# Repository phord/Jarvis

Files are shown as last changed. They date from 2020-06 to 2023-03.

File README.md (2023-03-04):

**Me:** Ok, Google. Stand up.<br/>
**Google Assistant:**  Ok. Raising your Jarvis desk.<br/>
**Desk:** _begins moving obediently_<br/>

# IoT Jarvis standup desk interface

**Notice:** This project probably will void your warranty.  Proceed at your own risk.

This is a project to add a computer interface to my [Jarvis stand-up desk from fully.com](https://www.fully.com/standing-desks/jarvis.html).
I reverse-engineered the interface between the desk handset and the desk controller box
to find out how they communicate. Then I wired an ESP8266 wifi module (like the [Huzzah
from Adafruit](https://www.adafruit.com/product/2471)) to a couple of RJ-45
jacks and plugged it all together.  Now I can snoop on the messages being sent between
the desk and the handset, inject my own messages to either one, and monitor the desk position
from the internet using the AdafruitIO MQTT dashboard interface.

It's pretty cool, but honestly, my motivation was to be able to lower the desk without getting
up to see the handset controller. The desk sits next to my couch at home. When I want to set
a drink on it while watching TV, it's inconvenient if I left it standing up.  "Ok, Google. Sit down"
The desk lowers, and I can put my drink down and continue watching Netflix. To be fair, I didn't need to
decode the serial interface for this because the buttons used for memory presets are sent on separate
signal lines. The serial protocol decoding was just for fun.

As a useless side-benefit, you can look back at my [desk's height history](https://io.adafruit.com/phord/feeds/jarvis.height) and see every time it moved up or down and [what preset was used](https://io.adafruit.com/phord/feeds/jarvis.preset) in the last 30 days.
And I can control my desk from anywhere on the internet, so I can lower it even if I'm not home, though that
seems like a bad idea.

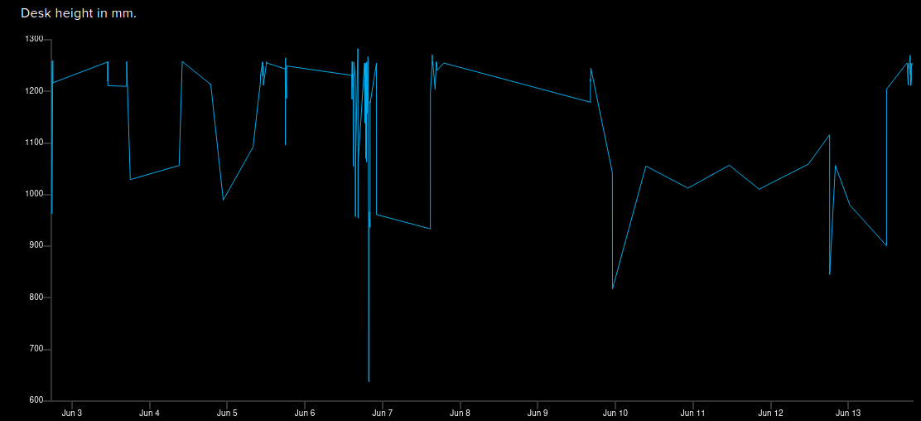
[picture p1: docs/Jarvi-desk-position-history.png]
Jarvis desk position history graph


Features so far:
* Reverse engineered the UART interface and most control messages
* Snoop on the messages being sent between the desk and the handset
* Read the handset buttons
* Telnet wifi interface for debug logging
* Simulate handset buttons (e.g. press 3)
* Monitor desk configuration
* Connected the desk to AdafruitIO's MQTT dashboard for monitoring
* Can control the desk position via the AdafruitIO dashboard
* Interfaced IFTTT to the AdafruitIO feed controlling my desk
* Added a Google Assistant command phrase to raise and lower my desk

Future things:
* Inject control messages to the UART to control and configure the desk
* Inject control messages to the UART to control the handset display
* Explore the handset to see what else it might be hiding
* Keep the handset display awake so buttons are always visible[1]
* Explore the _other_ UART control protocol the desk sometimes falls into
* Expose all handset controls so people can add memory presets to their cheap-model handsets.
* Expand the telnet interface to permit different log levels, message injection, etc.

[1] Sadly, you can't display random text on your display module, as far as I know.
But you could make a nice little 3-digit clock or something there, if you wanted.

# Software notes:

## Security configuration (REQUIRED)

You will need to edit the `local-config.h` file to include your own WiFi access credentials and your Adafruit IO
username and API key.

    // AdafruitIO credentials
    #define IO_USERNAME "your-adafruitio-id"
    #define IO_KEY "your-adafruitio-api-key-hex"

    // Wifi AP credentials
    #define WIFI_SSID "wifi-ssid"
    #define WIFI_PASS "wifi-password"

For your safety (and mine) this file is in the `.gitignore` file for this project to help prevent us from accidentally
committing password information to the project and sharing it with the world. If you want to keep this config file
history in your own local git repository, please be aware of this limitation.

## Board configuration (REQUIRED)

You will need to edit the pin definitions in `jarvis_pinouts.h` to match the GPIOs you used on your board. You will need
6 pins defined. You can use one of the existing layouts defined there by uncommenting the correct #define directive, or
you may choose your own pin layout by adding your own customized version with the `DEFINE_PINS` macro.

## Building the code

This code should be able to build with the [Arduino IDE](https://www.arduino.cc/en/software) or the [arduino-cli](https://www.arduino.cc/pro/cli) tool. You will need extra libraries installed to support your target board. This code is written for the ESP8266, so to
build it as-is, you would need the ESP8266 toolkit, for example. If you use the Adafruit.IO feed you will
also need to install the Adafruit IO library and its dependencies.

To build with arduino-cli, do this:

    arduino-cli compile -b esp8266:esp8266:oak .

## OTA Software Upload

The code here supports Over-the-Air (OTA) program upload using the ESP8266 "espota.py" tool or the ArduinoIDE.
Once a version of this code is booted and running on the board, future updates can be uploaded with the OTA update.

In the Arduino IDE, OTA upload can be done by changing the port from the serial port to the Jarvis (network) port
here:
    ArduinoIDE > Tools > Port : Jarvis
If the device is online and connected to your network, it should show up in the Port menu under "Network ports".

To upload using the espota utility:

    $HOME/.arduino15/packages/esp8266/hardware/esp8266/3.0.2/tools/espota.py -i jarvis.local -p 8266 -f Jarvis.ino.bin

## Telnet interface

The code runs a telnet interface for debug output. This is mostly for convenience, but it also frees up the serial port
pins for use as GPIO pins to connect to the desk.

Telnet to `jarvis.local` on port 23 to see the debug logs.

    telnet jarvis.local

## Board wiring

**WARNING: This is the part that probably voids your warranty.**

The 6 GPIO pins you chose on the ESP8266 board should be wired to the RJ-45 signal pins on your desk.
In addition, you will need to wire the RJ-45 GND pin (pin 3) to your controller ground, and for convenience
you can wire the RJ-45 VCC (pin 5) to your controller's VCC to power it when it's not connected to external power.

See [this discussion](https://github.com/phord/Jarvis/discussions/8) for notes on how I wired up my board.

# Technical notes
## Hardware

The Jarvis desk handset style I have is the touchpanel interface with memories.  You can surely use
the desk without this interface if you design your own, but you need to know the protocols.  I
will try to publish what I discovered through reverse-engineering here.

* Handset model: JCHT35M16-1
* Desk controller model: FullyCB2C-A

Note: Other desk owners have mentioned that the simple 2-button handset interface uses a different
desk controller (model: JCB35N2) but has the same electrical interface. However the serial interface uses
a different protocol. You can find some details in the [JCB35N2 controller protocol discussion](https://github.com/phord/Jarvis/discussions/4).
It's a bit exciting that the basic and advanced models both seem to support both protocols in some form, but so far
I don't know how to switch between them on either controller.

## Physical interface (RJ-45)

The interface from the handset to the controller is via an RJ-45 8-pin connector (like an ethernet
connector). The pins in the RJ-45 jack are numbered 1 to 8.

_Note: I don't know any official names for these signal lines, so I made these up myself._
_Any mistakes here about the meaning or use of these lines are mine._

Following are their usage on the desk:

| Pin | Label | Description
| --- | ----- | ---
|  1  |  HS3  | Handset control line 3 [1]
|  2  |  DTX  | Serial control messages from controller to handset [2]
|  3  |  GND  | Ground
|  4  |  HTX  | Serial control messages from handset to controller [2]
|  5  |  VCC  | Vcc (5vdc) supply from desk controller [3]
|  6  |  HS2  | Handset control line 2 [1]
|  7  |  HS1  | Handset control line 1 [1]
|  8  |  HS0  | Handset control line 0 [1]

[1] The pins (HS0, HS1, HS2, HS3) make up the "button-press" mux lines. See _HSx control lines_ below<br/>
[2] Serial port UART is 9600bps, 8 data bits, No parity, 1 stop bit<br/>
[3] 5VDC supply appears capable of driving at least 300ma<br/>
[4] All the signal lines have 5v pullups provided by the desk controller

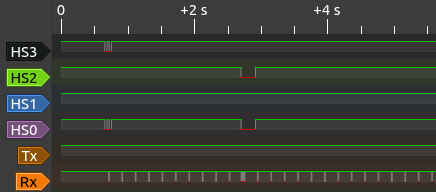
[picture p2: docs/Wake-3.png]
Interface signal showing "Memory" and "3" being pressed


_In this capture, I pressed "Memory" to wake the screen up, and then 3 to move the desk to position 3._

## Physical interface (RJ-12)

Some controllers such as the Jiecang JCB36N2CA fitted in recent Fully Jarvis models also offer an RJ-12 6-pin
connector (like a telephone jack), which is used for an [optional Bluetooth add-on](https://fccid.io/2ANKDJCP35NBLT/Internal-Photos/Internal-Photos-3727739).
Of the 6-pin connector, only the center 4 pins are required for the Bluetooth add-on, meaning an RJ-11 connector,
which is physically idential but has only 4 conductors populated, will work just fine.

The pins in the RJ-12 jack are numbered 1 to 6. Following are their usage on the desk:

| Pin | Label | Description
| --- | ----- | ---
|  1  |  NC | (unpopulated in Bluetooth add-on, pulled high by controller)
|  2  |  GND  | Ground
|  3  |  DTX  | Serial control messages from controller to handset
|  4  |  VCC  | Vcc (5vdc) supply from desk controller
|  5  |  HTX  | Serial control messages from handset to controller
|  6  |  NC | (unpopulated in Bluetooth add-on, pulled high by controller)

## Interfacing with 5 volts

The desk provides 5v pullups on all six signal lines. A "mark" is signaled by pulling the line low.

The ESP8266 microcontroller is only capable of outputting 3.3v on its GPIOs. But I don't need to pull
any of these pins high to 5v because the desk does that for me. I only need to pull these signals low
to 0.0v.

It is safe to _sink_ 5v on these GPIO pins on the ESP8266, so long as the carrier board doesn't
mind the extra voltage. Opinions vary on this topic, though. You may feel safer using a level shifter
or some transistor or diode assistance to pull these 5v signals low on your board. Doing this is beyond
my expertise, though, so I'm afraid I can't help you with this part if you choose to go this route.

## HSx control lines

On the mechanical desk control buttons, when you press the up button, one of the HS[0-2] lines is
pulled low. Similarly when you press the down button, another line is pulled low. When you
use a smart controller interface like the touch-screen model, multiple lines may be pulled
low simultaneously to indicate up to 7 different buttons.  If you combine the first three
lines' inverted logical signals, you will find a "button number" between 0 and 7 is possible.

Zero means no button is being pressed.  This is "open".

Note: HS0+HS3 is used to wake up the controller to send height information.

         Down  Up  1  2  3  4  M
    HS3                        X
    HS2               X  X  X
    HS1         X  X        X
    HS0    X       X     X     X

Translated into binary, these buttons send these codes:
| Button | Value | Notes
| --- | ----- | ---
| "Open" | 0 |
| Down | 1 |
| Up | 2 |
| 1 | 3 |
| 2 | 4 |
| 3 | 5 |
| 4 | 6 |
| *any*  | 9 |  Sent when display is touched while asleep. Always sent as two 30ms pulses.

## UART protocol

The Jarvis UART signaling protocol sends checksummed control packets consisting of between 6
and 9 bytes. All data is sent using 9600 bps, 8 data bits, no parity (9600/8N1). The desk controller
sends data on DTX; the handset sends data on HTX. Command packets are the same format on both.

    [address] [command] [length] [params] [checksum] [eom]

| Field | Octets  | Description
| --- | --- | ---
| ADDRESS  | 2  | Same value in both bytes; 0xF1 for Handset, 0xF2 for controller
| COMMAND  | 1  | See *KNOWN COMMANDS*
| LENGTH | 1  | Length of PARAMS bytes that follow (0 to 4 (??))
| PARAMS | LENGTH  | Omitted if LENGTH=0
| CHECKSUM | 1  | 8-bit sum of {COMMAND, LENGTH, PARAMS}
| EOM 0x7E | 1  | End of message (0x7E)

The address byte is repeated two times.  The desk controller always sends 0xF2 0xF2.
The handset always sends 0xF1 0xF1.

The PARAMS field consists of 0 to 3 bytes.  I haven't decoded all the meaning here. WIP

The checksum is the low-byte sum of the all the payload bytes.  In pseudocode,

     CHECKSUM = sum(COMMAND, LENGTH, PARAMS) % 0xFF

The EOM byte is always 0x7E.

I will use a shorthand to refer to these packets later. The desk controller packets will be
given as `CONTROLLER(COMMAND, PARAMS, ...)` and the handset packets will be given as
`HANDSET(COMMAND, PARAMS...)`.  `PARAMS` are given as `P0` for the first byte, `P1` for the second,
etc.  16-bit params are indicated like `{P0,P1}`. Optional params are shown in brackets.

For example, the `HANDSET(0x29)` message is sent from the handset to the desk.  It represents
this sequence of 6 bytes:

    F1  F1     29       00       29          7E
    ADDRESS    COMMAND  LENGTH   CHECKSUM    EOM

## Startup sequence

Smart handset sends a `NULL (0x00)` byte on first startup.  If no response is received from the
desk controller, it sends a 230ms BREAK signal followed by another `NULL` byte. If still no
response is received, it begins sending `HANDSET(0x29)` repeatedly.

## Known Commands (Handset)

_Note: I don't know any official names for these commands, so I made these up myself._
_Any mistakes here about the command usage or meaning are mine._
_All transmitted byte values are given in hex._

| Name | CMD  | Params | Description
| --- | ---- | --- | ---
| RAISE |  01  | 0 | Raise desk by one step
| | | |
| LOWER |  02  | 0 | Lower desk by one step
| | | |
| PROGMEM\_1  |  03  | 0 | Set memory position 1 to current height
| PROGMEM\_2  |  04  | 0 | Set memory position 2 to current height
| | | |
| MOVE\_1 |  05  | 0 | Move desk to memory position 1
| MOVE\_2 |  06  | 0 | Move desk to memory position 2
| | | |
| SETTINGS |  07  | 0 | Request all memory heights and settings;
| | | | On RJ-45, desk will respond with [25] [26] [27] [28] [0E] [19] [17] [1D] and [01]
| | | | On RJ-12, desk will respond with [25] [26] [27] [28] and [01]
| | | |
| UNKNOWN\_08 |  08  | 0 | Unknown. Desk will respond with [05]
| | | |
| UNKNOWN\_09 |  09  | 0 | Unknown. Desk will respond with [06]
| | | |
| UNKNOWN\_0C |  0C  | 0 | Maybe: Request physical limits of motion. Desk will respond with [07]
| | | |
| UNITS |  0E  | 1 | Set units to cm/inches
| | | | P0=0x00  Set units to CM
| | | | P0=0x01  Set units to IN
| | | |
| MEM\_MODE |  19  | 1 | Set memory mode
| | | | P0=0x00  One-touch mode
| | | | P0=0x01  Constant touch mode
| | | |
| UNKNOWN\_1C |  1C  | 0 | Unknown. Desk will respond with [1C]
| | | |
| COLL\_SENS  |  1D  | 1 | Set anti-collision sensitivity  (Sent 1x; no repeats)
| | | | P0=0x01  High
| | | | P0=0x02  Medium
| | | | P0=0x03  Low
| | | |
| UNKNOWN\_1F |  1F  | 0 | Unknown. Desk will respond with [1F]
| | | |
| LIMITS |  20  | 0 | Request limit report, desk will respond with [20] and if set [21] and [22]
| | | |
| SET\_MAX |  21  | 0 | Set max height; Sets max-height to current height
| | | |
| SET\_MIN |  22  | 0 | Set min height; Sets min-height to current height
| | | |
| LIMIT\_CLR  |  23  | 1 | Clear min/max height
| | | | P0=0x01  Clear Max-height
| | | | P0=0x02  Clear Min-height
| | | |
| PROGMEM\_3  |  25  | 0 | Set memory position 3 to current height
| PROGMEM\_4  |  26  | 0 | Set memory position 4 to current height
| | | |
| MOVE\_3 |  27  | 0 | Move desk to memory position 3
| MOVE\_4 |  28  | 0 | Move desk to memory position 4
| | | |
| WAKE |  29  | 0 | Poll message sent when desk doesn't respond to BREAK messages
| | | |
| CALIBRATE |  91  | 0 | Height calibration (Repeats 2x)
| | | | Desk must be at lowest position
| | | | Desk enters RESET mode after this
| | | |

## Known Responses (Desk)

_Note: I don't know any official names for these commands, so I made these up myself._
_Any mistakes here about the command usage or meaning are mine._
_All transmitted byte values are given in hex._

| Name | CMD  | Params | Description
| --- | ---- | --- | ---
| HEIGHT |  01  | 3 | Height report; P0=4 (mm?)
| | | | {P0,P1} = height in mm or tenths of inches
| | | | P2 = ??? (0x7 or 0xF seen so far)  Not units
| | | | Height from 240..530 is in inches
| | | | Height from 650..1290 is in mm
| | | |
| UNKNOWN\_05 |  05  | 2 | Unknown response to [08]. P0 and P1 have been observed as 00 00 or FF FF
| | | |
| UNKNOWN\_06 |  06  | 1 | Unknown response to [09]. P0 has been observed as 01
| | | |
| UNKNOWN\_07 |  07  | 4 | Maybe: Physical limits of motion. Response to [0C].
| | | | {P0,P1} = upper limit, {P2,P3} = lower limit (in mm)
| | | | Params have been observed as 05 14 02 8A, which would be 1300mm, 650mm
| | | |
| UNITS |  0E  | 1 | Report units setting
| | | | P0=0x00  Units set to CM
| | | | P0=0x01  Units set to IN
| | | |
| UNKNOWN\_17 |  17  | 1 | Unknown response to [07]. P0 has been observed as 01
| | | |
| MEM\_MODE |  19  | 1 | Report memory mode
| | | | P0=0x00  One-touch mode
| | | | P0=0x01  Constant touch mode
| | | |
| UNKNOWN\_1C |  1C  | 1 | Unknown response to [1C]. P0 has been observed as 0A
| | | |
| COLL\_SENS  |  1D  | 1 | Report anti-collision sensitivity
| | | | P0=0x01  High
| | | | P0=0x02  Medium
| | | | P0=0x03  Low
| | | |
| UNKNOWN\_1F |  1F  | 1 | Unknown response to [1F]. P0 has been observed as 00
| | | |
| LIMITS |  20  | 1 | Report which limits are set; response to [20] through [23]
| | | | P0=0x00  "Min/max cleared"
| | | | P0=0x01  "Only max-height set"
| | | | P0=0x10  "Only min-height set"
| | | | P0=0x11  "Min and max set"
| | | |
| SET\_MAX |  21  | 2 | Report max-height; [P0,P1] = max-height
| | | |
| SET\_MIN |  22  | 2 | Report min-height; [P0,P1] = min-height
| | | |
| LIMIT\_STOP |  23  | 1 | Min/Max reached. Not sent on RJ-12.
| | | | P0=0x01  "Max-height reached"
| | | | P0=0x02  "Min-height reached"
| | | |
| POSITION\_1 |  25  | 2 | Memory position 1 height. Response to [07].
| POSITION\_2 |  26  | 2 | Memory position 2 height. Response to [07].
| POSITION\_3 |  27  | 2 | Memory position 3 height. Response to [07].
| POSITION\_4 |  28  | 2 | Memory position 4 height. Response to [07].
| | | | {P0, P1} = height in mm or tenths of inches
| | | |
| RESET |  40  | 0 | Indicates desk in RESET mode; Displays "RESET"
| | | |
| REP\_PRESET |  92  | 1 | Moving to Preset location. Not sent on RJ-12.
| | | | P0=[4,8,10,20] mapping to presets [1,2,3,4]

## Height report

The desk controller responds to the handset by sending a display message containing the current
desk height. It sends this several dozen times while the display is on.  The height is encoded
as a two-byte word (HI, LOW) which make up the desk's height.  The units are in millimeters or
tenths of inches depending on the configuration UNITS setting. The packet looks like this:

    CONTROLLER(0x01, HI, LOW, 0x07)

For example, to indicate 128.6cm (1286mm), the desk sends `CONTROLLER(0x01, 0x05, 0x06, 0x07)`,
because 0x0506 = 1286 in decimal.  I don't know what the third parameter is here (0x07).  Sometimes
it's 0x0F.  More experimenting is needed.

## Memory setting

Memories are programmed by sending one of the `PROGMEM_*` commands to the controller.  Each
command takes no parameters but sets the memory to the current height of the desk.

The desk does not acknowledge the setting.

## Preset buttons observation

When a Preset button is pressed (not in a programming mode) the lines `HS0`..`HS3` are signaled as
shown above in *HSx control lines*. Notice that the binary pattern flagged in those pins maps
preset button 1 to 0x03, 2 to 0x04, 3 to 0x05 and 4 to 0x06.

The command codes to set these presets are mapped similarly, but not identically:

    PROGMEM_1 = 0x03, PROGMEM_2 = 0x04, PROGMEM_3 = 0x25 and PROGMEM_4 = 0x26

Why not the same?  Is it because buttons 3 and 4 were added on later, but commands 0x05/0x06 were already used?
Is bit 5 (0x20) used to signal something special?

## Configuration commands

See the table above for the short version.  Each command may or may not be sent multiple times and
have a different stream of responses from the other side.  I'll try to document my findings about
these anomalies here later.

# DigiStump Oak notes

Robodesk Jarvis v1 was built with a DigiStump Oak. I don't recommend these boards since they seem to have stopped
making them a few years ago. But I leave these notes here for myself:

Install using the ESP8266 Community package here: https://arduino.esp8266.com/stable/package_esp8266com_index.json

First time programming: Connect P2 to GND to start Oak in serial program mode

Thereafter, use the OTA Software Upload described above.

# Related projects

These other projects also aim to decode the Jarvis and/or Uplift protocols.  Some of them got their start from
this project, but they may have added more info and other desks since the time I wrote this.

[Upsy Desky](https://github.com/tjhorner/upsy-desky) (originally [wifi standing desk controller](https://www.tindie.com/products/tjhorner/wifi-standing-desk-controller/))
A [nice custom build](https://www.youtube.com/watch?v=DTJSREjWH7Y) by David Zhang.
A [thread on integrating ESPHome](https://community.home-assistant.io/t/desky-standing-desk-esphome-works-with-desky-uplift-jiecang-assmann-others/383790/16) with Jarvis/Desky/Uplift, etc.
[RMcGibbo's home build](https://github.com/rmcgibbo/Jarvis)

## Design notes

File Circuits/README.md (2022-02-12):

# Circuit boards

Multiple circuit board designs are available here to build a Jarvis Desk interface.  Only one is needed, but you should
choose one appropriate to your needs and work from there.

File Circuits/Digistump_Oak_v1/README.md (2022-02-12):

# Pebble Netlist for Digistump Oak V1

This circuit includes a 6-pin FTDI header for serial programming the Oak board.  This is only needed
because the Oak did not have a built-in UART interface on the USB connector.

This circuit is wired by hand.  There may be mistakes.  Please check your results against the code carefully.

To use view or modify this netlist, load it into the PEBBLE Picaxe Electronic Bread Board Layout Emulator.
You can find this online in several places to run locally or on the web.

The one I used is here: [PEBBLE v3.1](http://pebble.my-board.org/P_for_FF.html)

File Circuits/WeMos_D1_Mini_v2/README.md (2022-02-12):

# Printed circuit board using WeMos D1 Mini

I routed and drew this circuit with [Fritzing](https://fritzing.org/download/) and ordered PCBs from [AISLER](https://aisler.net/).
The boards arrived in about 2 weeks.

Be sure to use the JARVISDESK_WEMOS_D1MINI_V2 configuration in `jarvis_pinouts.h`.

Other parts you will need to complete this board:
- 2 x [RJ45 8-Pin Connectors Sparkfun #PRT-00643](https://www.sparkfun.com/products/643)
- 1 x [WeMos D1 Mini clone](https://www.wemos.cc/en/latest/d1/d1_mini.html) [Amazon](https://www.amazon.com/MakerFocus-NodeMcu-Development-ESP8266-Compatible/dp/B07KW54YSK)
- 1 x RJ-45 patch cable [Amazon](https://www.amazon.com/Monoprice-Cat6-Ethernet-Patch-Cable/dp/B003L1AET2)

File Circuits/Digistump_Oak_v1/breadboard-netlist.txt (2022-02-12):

Terminal||38|116|1||TS?||8|4|Terminals||terminal_481
Terminal||38|143|1||TS?||8|4|Terminals||terminal_481
Terminal||550|143|1||TS?||9|4|Terminals||terminal_491
Terminal||550|363|1||TS?||9|4|Terminals||terminal_491
Wire||184|400|11||21|#FFFF00|16|11||10|
Wire||49|152|11||11|#000000|1|11||10|
Wire||748|17|21||11|#000000|3|11||10|
Wire||155|44|21||11|#FF0000|2|11||10|
Wire||101|17|21||11|#000000|3|11||10|
Wire||425|17|21||11|#000000|3|11||10|
Wire||236|209|21||13|#FFFF00|3|11||10|
Wire||49|198|12||21|#FFFF00|25|11||8|
Wire||76|183|13||11|#3253FF|10|11||10|
Wire||130|210|13||11|#A233C3|7|11||8|
Wire||209|209|21||13|#FFFF00|3|11||10|
Wire||182|209|21||13|#FFFF00|3|11||10|
Wire||750|345|11||11|#999999|3|11||10|
Wire||775|44|21||11|#FF0000|2|11||10|
Wire||211|345|11||21|#FFFF00|16|11||10|
Wire||238|320|13||21|#FFFF00|16|11||10|
Switch||802|370|3||SW?|1||1|Switch||switch_113
Wire||802|209|21||11|#000000|3|11||10|
Wire||615|125|11||11|#999999|8|11||10|
Switch||802|150|3||SW?|1||1|Switch||switch_113
Wire||802|17|21||11|#000000|3|11||10|
Terminal||281|116|1||TS?||6|4|Terminals||terminal_461
Wire||265|281|12||11|#999999|18|11||10|
Wire||253|209|22||11|#999999|4|11||10|
Wire||371|44|21||11|#FF0000|2|11||10|
Wire||346|210|13||11|#3253FF|12|11||10|
Wire||319|171|12||11|#A233C3|14|11||8|
BREADBOARDSTYLE=BB12
SHOWTHETOPAREA=false

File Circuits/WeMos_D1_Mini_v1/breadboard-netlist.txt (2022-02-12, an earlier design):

Terminal||38|438|1||TS?||8|4|Terminals||terminal_481
Note||30|524|2||||2||RJ-45 Connectors||NOTEPAD_22
Wire||101|312|21||11|#000000|3|11||10|
Wire||155|339|21||11|#FF0000|2|11||10|
Terminal||631|411|1||TS?||8|4|Terminals||terminal_481
Terminal||631|658|1||TS?||8|4|Terminals||terminal_481
Note||706|516|2||||2||wifi-[Wemos D1 Mini]-usb||NOTEPAD_22
Wire||829|339|21||11|#FF0000|2|11||10|
Wire||802|312|21||11|#000000|3|11||10|
Wire||76|478|13||11|#3253FF|24|11||10|
Wire||130|466|12||11|#A233C3|23|11||10|
Wire||49|383|12||11|#FFFF00|24|11||10|
Wire||182|504|21||11|#FFFF00|3|11||10|
Wire||209|504|21||11|#FFFF00|3|11||10|
Wire||236|504|21||11|#FFFF00|3|11||10|
Wire||184|695|11||11|#FFFF00|21|11||10|
Wire||211|640|11||11|#FFFF00|18|11||10|
Wire||238|612|11||11|#FFFF00|18|11||10|
BREADBOARDSTYLE=BB12
SHOWTHETOPAREA=true

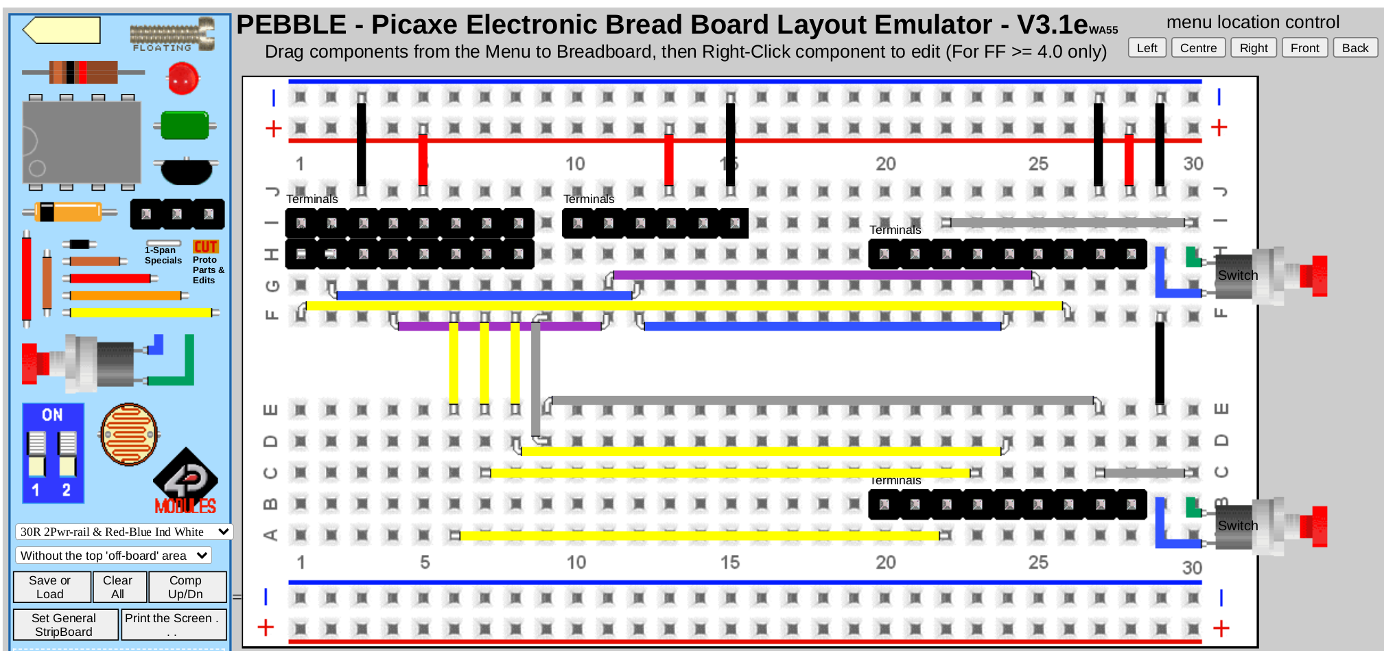
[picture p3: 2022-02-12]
Circuits/Digistump_Oak_v1/DigistumpOak_v1.png

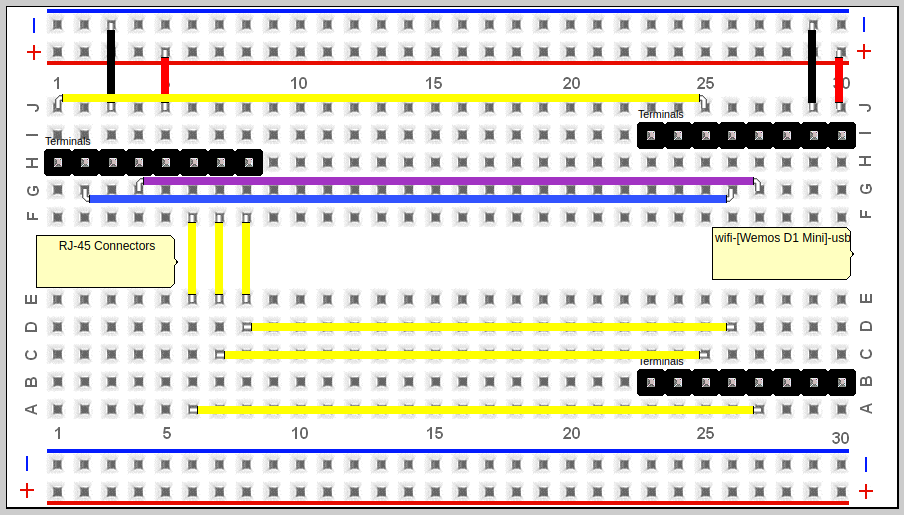
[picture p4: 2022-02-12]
Circuits/WeMos_D1_Mini_v2/WeMosD1Mini_v1.png

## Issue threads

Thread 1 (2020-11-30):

More info on how this was connected

lemiesz, 2020-11-30:
Hi,

Forgive me I am not vert experience with IoT controllers. Could you possible give me some more detail on how you connected the wifi module to your desk, if you still have it could I see a picture?

Also, do you think it would be possible for me to prototype something like this with a direct ethernet connection from my laptop.

malfroid, 2020-12-03:
I am also very much interested on how to practically connect a [V3 Nodemcu-CH340 board](https://nl.aliexpress.com/item/32665100123.html?spm=a2g0s.9042311.0.0.40694c4d0S8hyg) (based on ESP8266 ES-12E) through 8P8C connector and UTP cable to the Fully Jarvis components (desk handset, desk controller box).

Do you strip the different wires in an UTP cable and solder to the ESP8266 pins?

How do you connect three UTP cables coming from desk handset, the desk controller box and the new components (ESP8266)? Do you use some kind of Ethernet hub for this?

phord, 2020-12-08:
At first I used some stripped spare CAT-5 cable to make it easier to reverse-engineer the signal pins from the Jarvis controller.  I brought these out onto an 8-pin connector on a breadboard and attached my logic analyzer to do signal captures.  I use the [USB Logic Analyzer](https://www.sparkfun.com/products/15033) from Sparkfun with [sigrok/PulseView](https://learn.sparkfun.com/tutorials/using-the-usb-logic-analyzer-with-sigrok-pulseview) on Linux.

After that, I connected an ESP8266 to the same breadboard and started tinkering from there.  It was rather ugly.

I started to design a proper circuit in some EDA tool, but I'm terrible at that. So I took the quick route one afternoon and drew some traces in an online [Pebble](http://pebble.my-board.org/P_for_FF.html) tool.  I'd post the netlist here, but it's not terribly useful unless you have the same board I do.  Also, I'm not sure it's correct; I only used it as a guide.  I ended up moving things further apart later and I left off the boot-mode switches.
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

Columns 1-8:  RJ-45 connectors
Columns 10-15: FTDI serial programming interface
Columns 20-28: Digistump Oak ESP-8266 daughterboard

I didn't use a NodeMCU module for this, but I easily could.  I used an ESP8266-based Digistump Oak board because I have a few handy from their kickstarter a few years ago. I don't recommend them, otherwise, since their plans got shanghaied by a poorly executed partnership with Particle.io.

I breadboarded it on my bench to get it working.  Later I converted that to the Pebble breadboard layout above just so I could double-check things and play with other ideas.

The interface is really simple.  I draw power from the Jarvis controller itself.  There is almost always enough current to drive the ESP8266.  I have had some occasional problems that might be caused by brownouts, but I'm still not sure.

The only clever part worth mentioning is that I mounted two RJ-45 jacks on the board in a pass-thru configuration.  That is, there are two RJ-45's mounted together, one is rotated 180 degrees on two axes, so the pins all connect "straight through".  This is easier to see on the next picture.
* Conn1.Pin1 goes to Conn2.Pin1
* Conn1.Pin2 goes to Conn2.Pin2
* ...
* Conn1.Pin8 goes to Conn2.Pin8

Look at the pair of connectors at H1-8 and I1-8 on the Pebble breadboard above.  One of those is actually below the board pointing down instead of up.  Each pair of pins on those two connectors is electrically connected (because of the breadboard). Then I mounted one RJ-45 to the top set of pins and the other one to the bottom set of pins.  The bottom connector is rotated and turned around to face the opposite direction so the pins all connect as described.

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

Then I plug the Jarvis Handset's RJ-45 cable into one of these (it doesn't matter which one), and I use a regular 8-pin network patch cable to connect the module to the Jarvis controller itself.

By the way, the handset is optional.  You could drive it all from the ESP8266.  The passthrough works well, though.

Note: If you get the [RJ-45 breakout board from SparkFun](https://www.sparkfun.com/products/716), it makes it easy to stack these on headers.  But be careful when assembling it because Pin-8 is mis-labeled as Pin1 and vice-versa.  Read the user comments on the product page to see more details.

phord, 2020-12-08:
Here's another view of the board in the same orientation as the Pebble image.
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
I found I needed more space for the FTDI connector to fit because the FTDI-board is wider than the connector.  So I moved the Oak pins over two more places and removed the switches.  I think I had the serial Tx/Rx pins reversed on the Oak, too.  Even though you can't see it here, the green and blue wires that go to pins 24/25 are backwards.

phord, 2020-12-08:
> Also, do you think it would be possible for me to prototype something like this with a direct ethernet connection from my laptop.
@lemiesz The RJ-45 connector here is not used as an Ethernet connection.  The electrical signals are all different.  So no, you cannot connect this to your laptop's Ethernet port.

Closed 2020-12-08.

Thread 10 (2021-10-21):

The micro controller does not start correctly if wired to the handset

Viroide, 2021-10-21:
Hello,

_Probably this is not an issue of the software in this repo, I just need help with this._ Move to discussions if you think that suits more.

HandSet: JCHT35M
Controller: JCB36N2CA
Microcontroller: ESP8266 mod 12F

When I have all set up everything works correctly, but if I shut down the table, when I turn it on the micro-controller does not boot correctly. The led does not blink at all and the throws an exception throw the serial port. In order to work again I need to unplug both RJ45 wire and plug first the one from the controller, once the board is booted I can plug the handset RJ45.

Any idea why this happens?

phord, 2021-10-23:
I suspect it's gpio15. This point needs to be pulled low during boot. You might be able to use it still if you put a capacitor to ground there, but that may also prevent you from using it for serial comms.

Try moving RX to a different gpio.

https://www.esp8266.com/viewtopic.php?p=41723

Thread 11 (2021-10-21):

Ground loops

Yatekii, 2021-10-21:
Hi, thanks a lot for the great work!

This is not protocol related but maybe you debugged this enough to tell me: Is the UART interface of the desk isolated? Or how did you make that work? I guess you connected VCC and GND on the RJ45 to your devkit but also via USB for programming the devkit.

I am trying to control my desk via USB (FTDI) and I am afraid I light it on fire when there is ground shifting and bad loops involved (I managed to burn quite a few devices aleady in the past).

Could you provide some insight here; would be much appreciated!

Best,
Noah

phord, 2022-01-23:
I did connect the FTDI and the controller to the desk's GND and VCC.  This is necessary for a common signalling interface. And I am able to program the controller this way, but I don't remember if I tried that while it was connected to the desk.

All of the signals on the desk are TTL levels only, including the UART.  I treat them all as digital signals and haven't had any problems. The UART signals on the FTDI adapters are also TTL signals. I'm not sure what you mean about a ground loop in this context. But that may be because I am not real competent with electronics.  I only dabble.  As long as you don't short the Vcc pin from the desk to ground, I _think_ you'll be ok.  But I can't make any guarantees.

That's an interesting idea to use the FTDI to control the desk. I guess you can configure all the desk settings with serial commands. I don't know if you have enough pins to move the desk up and down, though.

Yatekii, 2022-01-23:
Hey :)

I had no issues at all with GND :) Tho I never made my desk move :( After my tries it was severely missconfigured and behaved oddly for weeks (only going 10cm up and then back down the same amount when holding up and vice versa). This persisted even through a reset. One day it was resolved.

To be honest, I did not quite make sense of bits of your protocol even tho the docs are quite nice :) I never got any response from the desk :(

The FTDI was merely for trying to communicate with the desk. In the end I would have made a custom PCB :) But I never got to the end of the prototyping phase. I guess ultimately I'd want an OSC on it to see what's happening.

phord, 2022-01-24:
Were you sending commands to the desk or just trying to receive data from the desk?  I guess if you messed up the desk config, you must have been trying to talk to it. And it sounds like you were partially successful if your data had some effect (even if it was a bad effect.) :-)

Here's what I see on the DTX pin on my desk right now:
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

I'm using a $20 logic analyzer to read that, but I also built one from an ESP8266 a while back.

Every message from the desk starts with "F2 F2".  The command is "01" - report height.  There are "03" parameter bytes following.  The reported height is 0x040E, or 1038mm.  I don't know what the third byte means (0x0f).  0x25 is the checksum, and 0x7E is end-of-message marker.

Not sure if that helps.

Closed 2023-06-09.

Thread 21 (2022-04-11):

A few qustions about commands

kquinsland, 2022-04-11:
Hi!

Thanks a ton for your work on this. I am working on porting your work to ESPHome and have managed to get the basics working: I can request the motor move to a preset.

I was wondering if there was a way to inquire about certain things rather than SET them. Almost all of the commands you've documented cover SETTING/CLEARING things.

How does the remote get the motor controller to respond with the height? I have used your notes to decode the height ... when it's transmitted. I want to get the motor controller to send this information on command, though.

I can keep spamming the `WAKE` `0x29` command and this will light the remote buttons up. The screen will be blank for a few seconds. I suspect that it's waiting for a height report and - after some timeout period of a few seconds - the remote falls back to just displaying the "fully" logo. It will display the logo until I stop spamming the WAKE commands.

Likewise, is there a way to inquire about the units without having to issue the `0x0E` command?

maraid, 2022-05-25:
Hi @kquinsland,

I think I can answer these to you.

_How does the remote get the motor controller to respond with the height?_

My experience is that the controlbox will never shut up really. If you send any command it'll spam a couple dozen of height reports back to you. Thus the initial 0x00 empty message. If you don't get anything back from it, then there's probably something wrong with the communication. Check the wiring.

_Is there a way to inquire about the units without having to issue the 0x0E command?_

Try 0x07. I spent some time reverse engineering more commands. The controlbox answers to 0x07 with:

0x25 - PresetRaw1
0x26 - PresetRaw2
0x27 - PresetRaw3
0x28 - PresetRaw4
0x0E - Units
0x19 - TouchMode
0x17 - KillMode (Anti-collision enabled)
0x1D - Sensitivity

Raw presets are just motor positions, they have to be converted to units.

Sorry for the self-advertisement but you can find more information about extra commands in [the project](https://github.com/maraid/Jarvis) I'm building:

kquinsland, 2022-06-03:
Few extra delays, but I've finally gotten my stuff out: https://github.com/kquinsland/fully_jarvis_esphome

I've starred / followed your repo @maraid. Looking forward to a simpler ESPHome component that uses UART only... which - hopefully - should solve some of the issues I have in my own code.

maraid, 2022-06-04:
Hi!
Good to hear that you haven't given up. Feel free to take anything from what I've done. I cannot access the repo you linked, is it private maybe?

I'm not planning on creating a proper ESPHome component and it's kind of hacky right now as you can see in the [yaml](https://github.com/maraid/Jarvis/blob/master/jarvis.yaml).  I might create a better HA card because it is pretty basic right now.
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

Good luck with your project and let me know if I can be of any help.

kquinsland, 2022-06-04:
> . I cannot access the repo you linked, is it private maybe?

It was! Thanks for catching that :).

> I'm not planning on creating a proper ESPHome component

Sorry to hear that. You should re-consider as it's not much more work beyond what you've already done to get the c++/h files included. Really, it's just some python which helps ESPHome understand how to validate the yaml and how to pass off the sensor/entity IDs to your code.

Feel free to use the esphome component in my repo as a starting point.  I got some help from this guy on the ESPHome discord and used the `desky` component as a reference of sorts: https://github.com/ssieb/custom_components/tree/master/components/desky

-----

Looking at your yaml, what's the difference between these two:

```yaml
  - platform: template
    name: "$name Height"
    id: height_number
    optimistic: false
    min_value: 1
    max_value: 1800
    step: 10
    set_action:
      - lambda: (*reinterpret_cast<JarvisDesk*>(id(desk))).move(x);
  - platform: template
    name: "$name Offset"
    id: offset_number
    optimistic: true
    min_value: 1
    max_value: 1800
    step: 1
    set_action:
      - lambda: (*reinterpret_cast<JarvisDesk*>(id(desk))).setOffset(x);
 ```

Does the 'move' command work precisely? That's the biggest "i want to improve" from my current implementation: https://github.com/kquinsland/fully_jarvis_esphome/blob/main/components/fully_jarvis_cb2c/fully_jarvis_cb2c.cpp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

maraid, 2022-06-06:
> Feel free to use the esphome component in my repo as a starting point.
Thanks. It really doesn't seem all that difficult as I imagined.

> Looking at your yaml, what's the difference between these two:
Height is what's shown on the display. Offset is what you would set with the calibration menu. In other words the lowest position of the desk. The upper limit for the offset is 65535 not 1800 but it would be pointless to set it anything beyond the displayable range.

> Does the 'move' command work precisely?
Mostly. I'm using centimeters and there's a slight problem with it. Whenever the desk moves upwards it stops 2 mm early. I couldn't figure out the reason so I just corrected it like so and it works.
(I didn't really test anything using inches.)

```cpp
void JarvisDesk::move(uint16_t height)
{
    // Hysteresis correction
    if (height > mHandset.getLastReportedHeight())
        height += 2;
    sendMessage(SerialMessage(CommandFromHandsetType::MoveTo,
                              static_cast<uint16_t>(height)));
}
```

kquinsland, 2022-06-06:
> Thanks. It really doesn't seem all that difficult as I imagined.

Right? The ESPHome docs are lacking on the 'getting started' front which is why my first several custom components were done the "manual include" way.  For better or worse, I 'reverse engineered' a lot of the python by cloning the esphome repo locally so I could study other components to get an idea for how Voluptuous had been used/extended and how to write the yaml -> c++ linking functions so entity IDs and the like are properly passed into your C code.

> I see what issues you had with setting the height precisely. This command definitely solves that. It does the deceleration the same as the memory buttons.

**AWESOME**. I know it's such a small thing, but it bugs me so much that I had to YOLO it with the precise height 'go to' command. I always assumed that there would be a UART command for it but didn't have the time/effort to properly sus it out.

I guess I'm still confused about what the offset would be used for. The only thing that comes to mind is if you wanted to program in the height of a desk / work surface so the display would indicate the height of the desk top and not the height of the motor/frame that the desk rests ontop of.

Closed 2022-06-03.

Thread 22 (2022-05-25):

More reverse engineering

maraid, 2022-05-25:
Hi @phord,

Firstly, thank you for the huge amount of information you shared here. With the help of your repository [I created a project](https://github.com/maraid/Jarvis) for Home Assistant specifically. It includes packet capturing, injecting, bug exploiting etc...

I spent quite some time fuzzing the protocol and a number of new commands came to light. I want to return the favor by sharing my findings with you. I hope it'll come in handy if you start implementing the missing features.

I was not sure how to contact you. If you're still planning to continue the development of your project and decide to incorporate some of my findings then feel free to reach me with any questions about them.

Regards,
maraid

phord, 2022-05-25:
Nice work!  That's a cool find about the control lines being optional.  That would make my circuit a lot simpler.  :-)

I have tinkered with the code some more a couple of times, but I only did useless housekeeping.  The code in my project is a real mess.  It represents what I found as I worked through it, mostly, so no decent design goals. I started cleaning it here and there but I got distracted by trying to meld in my latest ESP-common library, and... well, there was no reason for that.

Thanks for sharing the details.  I also want to have an always-on display and control of the display messages.  I'm convinced it will only display numbers and hard-coded errors on command, but maybe you'll find out different.  If I get time, I will try to incorporate your expanded command info into my project, too.

phord, 2022-05-25:
In your document, [this cell](https://docs.google.com/spreadsheets/d/1GKZfDFljVX4eQBMawq0-Rc8t0x8V6gjQ5BgAYngPYTo/edit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) has a couple of typos, I think.

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

Closed 2022-06-04.

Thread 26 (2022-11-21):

Readout not working

Karuption, 2022-11-21:
I was able to set up my 8266 to communicate with Adafruit and it will move my desk, however, I cannot get debug telemetry from the telnet server. I modified slightly to run report() with the preset command handle and it shows:

Height: 0
Preset: 0
Keys: 0

My desk is weighted on one side and needs calibrating often. I was hoping to figure out when it shows error and ASR and handle MQTT messages some other way. Any assistance on detecting this and getting the debug output would be great.

phord, 2022-11-28:
Sounds like your UART isn't working right.  Can you confirm the data pins are sending data somehow?  Do you have an o-scope or a logic analyzer?

Karuption, 2022-12-27:
I did some troubleshooting and it is getting the UART value, but it is not prefixed with 0xF1. All the desk serial object is picking up the 1 1 0 height information repeating with the last receipt is . It is not moving from SYNC.

phord, 2022-12-27:
Do you have the same controller?  There is [another serial data "mode" observed](https://github.com/phord/Jarvis/discussions/4) coming from the controller sometimes.  Maybe your controller is using that mode.  Read the discussion there to see if it matches what you see.

If so, you'll probably need to make quite a few changes in my code to get it to work.  And it won't be easy. This code was pretty sloppy; it is mostly a reverse-engineering exercise and some MQTT messaging.

Karuption, 2022-12-28:
I guess that it is the other one, JCB35N2-PA32-V2. However, I did order it with a programmable keypad. It seems like this other protocol is a lot simpler. My wake sends F5 then 1 1 0 FC (where 0 + FC is the height in inches) a ton of time then ends the stream with 1 5.

In my fork, I added serial commands to be able to set preset as well as clear error and re-level. looks like I will have to adopt/implement the other protocol to get the height information. I am not a C++ dev, but would you be interested in a PR to what I can fit in?

Desk wake output:
`Trying 192.168.x.x...
Connected to 192.168.x.x.
Escape character is '^]'.
Connected to Jarvis
F5
1
1
0
FC
1
1
0
FC
1
1
0
FC
1
1
0
FC
1
1
1
1
0
FC
1
1
0
FC
1
1
0
FC
1
1
0
FC
1
1
0
FC
1
1
0
FC
1
1
0
FC
1
1
0
FC
1
1
0
FC
1
1
0
FC
1
1
0
FC
1
1
0
FC
1
1
0
FC
1
1
0
FC
1
1
0
FC
1
1
0
FC
1
1
0
FC
1
1
0
FC
1
1
0
FC
1
1
0
FC
1
1
0
FC
1
1
0
FC
1
1
0
FC
1
1
0
FC
1
1
0
FC
1
1
0
FC
1
1
0
FC
1
1
0
FC
1
1
0
FC
1
1
0
FC
1
1
0
FC
1
1
0
FC
1
1
0
FC
1
1
0
FC
1
1
0
FC
1
1
0
FC
1
1
0
FC
1
1
0
FC
1
1
0
FC
1
1
0
FC
1
1
0
FC
1
1
0
FC
1
1
0
FC
1
1
0
FC
1
1
0
FC
1
1
0
FC
1
1
0
FC
1
1
0
FC
1
1
0
FC
1
1
0
FC
1
1
0
FC
1
1
0
FC
1
1
0
FC
1
1
0
FC
1
1
0
FC
1
1
0
FC
1
1
0
FC
1
1
0
FC
1
1
0
FC
1
1
0
FC
1
1
0
FC
1
1
0
FC
1
1
0
FC
1
1
0
FC
1
1
0
FC
1
1
0
FC
1
1
0
FC
1
1
0
FC
1
1
0
FC
1
1
0
FC
1
1
0
FC
1
1
0
FC
1
1
0
FC
1
1
0
FC
1
1
0
FC
1
1
0
FC
1
1
0
FC
1
1
0
FC
1
1
0
FC
1
1
0
FC
1
1
0
FC
1
1
0
FC
1
1
0
FC
1
1
0
FC
1
1
0
FC
1
1
0
FC
1
1
0
FC
1
1
0
FC
1
1
0
FC
1
1
0
FC
1
1
0
FC
1
1
0
FC
1
1
0
FC
1
1
0
FC
1
1
0
FC
1
1
0
FC
1
1
0
FC
1
1
0
FC
1
1
0
FC
1
1
0
FC
1
1
0
FC
1
1
0
FC
1
1
0
FC
1
1
0
FC
1
1
0
FC
1
1
0
FC
1
1
0
FC
1
1
0
FC
1
1
0
FC
1
1
0
FC
1
1
0
FC
1
1
0
FC
1
1
0
FC
1
1
0
FC
1
1
0
FC
1
1
0
FC
1
1
0
FC
1
1
0
FC
1
1
0
FC
1
1
0
FC
1
1
0
FC
1
1
0
FC
1
1
0
FC
1
1
0
FC
1
1
0
FC
1
1
0
FC
1
1
0
FC
1
1
0
FC
1
1
0
FC
1
1
0
FC
1
1
0
FC
1
1
0
FC
1
1
0
FC
1
1
0
FC
1
1
0
FC
1
1
0
FC
1
1
0
FC
1
1
0
FC
1
1
0
FC
1
1
0
FC
1
1
0
FC
1
1
0
FC
1
1
0
FC
1
1
0
FC
1
1
0
FC
1
1
0
FC
1
1
0
FC
1
1
0
FC
1
1
0
FC
1
1
0
FC
1
1
0
FC
1
1
0
FC
1
1
0
FC
1
1
0
FC
1
1
0
FC
1
1
0
FC
1
1
0
FC
1
1
0
FC
1
1
0
FC
1
1
0
FC
1
1
0
FC
1
1
0
FC
1
1
0
FC
1
1
0
FC
1
1
0
FC
1
1
0
FC
1
1
0
FC
1
1
0
FC
1
1
0
FC
1
1
0
FC
1
1
0
FC
1
1
0
FC
1
1
0
FC
1
1
0
FC
1
1
0
FC
1
1
0
FC
1
1
0
FC
1
1
0
FC
1
1
0
FC
1
1
0
FC
1
1
0
FC
1
1
0
FC
1
1
0
FC
1
1
0
FC
1
1
0
FC
1
1
0
FC
1
1
0
FC
1
1
0
FC
1
1
0
FC
1
1
0
FC
1
1
0
FC
1
1
0
FC
1
1
0
FC
1
1
0
FC
1
1
0
FC
1
1
0
FC
1
1
0
FC
1
1
0
FC
1
1
0
FC
1
1
0
FC
1
1
0
FC
1
1
0
FC
1
1
0
FC
1
1
0
FC
1
1
0
FC
1
1
0
FC
1
1
0
FC
1
1
0
FC
1
1
0
FC
1
1
0
FC
1
1
0
FC
1
1
0
FC
1
1
0
FC
1
1
0
FC
1
1
0
FC
1
1
0
FC
1
1
0
FC
1
1
0
FC
1
1
0
FC
1
1
0
FC
1
1
0
FC
1
1
0
FC
1
1
0
FC
1
1
0
FC
1
1
0
FC
1
1
0
FC
1
1
0
FC
1
1
0
FC
1
1
0
FC
1
1
0
FC
1
1
0
FC
1
1
0
FC
1
1
0
FC
1
1
0
FC
1
1
0
FC
1
1
0
FC
1
1
0
FC
1
1
0
FC
1
1
0
FC
1
1
0
FC
1
1
0
FC
1
1
0
FC
1
1
0
FC
1
1
0
FC
1
1
0
FC
1
1
0
FC
1
1
0
FC
1
1
0
FC
1
1
0
FC
1
1
0
FC
1
1
0
FC
1
1
0
FC
1
1
0
FC
1
1
0
FC
1
1
0
FC
1
1
0
FC
1
1
0
FC
1
1
0
FC
1
1
0
FC
1
1
0
FC
1
1
0
FC
1
1
0
FC
1
1
0
FC
1
1
0
FC
1
1
0
FC
1
1
0
FC
1
1
0
FC
1
1
0
FC
1
1
0
FC
1
1
0
FC
1
1
0
FC
1
1
0
FC
1
1
0
FC
1
1
0
FC
1
1
0
FC
1
1
0
FC
1
1
0
FC
1
1
0
FC
1
1
0
FC
1
1
0
FC
1
1
0
FC
1
1
0
FC
1
1
0
FC
1
1
0
FC
1
1
0
FC
1
1
0
FC
1
1
0
FC
1
1
0
FC
1
1
0
FC
1
1
0
FC
1
1
0
FC
1
1
0
FC
1
1
0
FC
1
1
0
FC
1
1
0
FC
1
1
0
FC
1
1
0
FC
1
1
0
FC
1
1
0
FC
1
1
0
FC
1
1
0
FC
1
1
0
FC
1
1
0
FC
1
1
0
FC
1
1
0
FC
1
1
0
FC
1
1
0
FC
1
1
0
FC
1
1
0
FC
1
1
0
FC
1
1
0
FC
1
1
0
FC
1
1
0
FC
1
1
0
FC
1
1
0
FC
1
1
0
FC
1
1
0
FC
1
1
0
FC
1
1
0
FC
1
1
0
FC
1
1
0
FC
1
1
0
FC
1
1
0
FC
1
1
0
FC
1
1
0
FC
1
1
0
FC
1
1
0
FC
1
1
0
FC
1
1
0
FC
1
1
0
FC
1
1
0
FC
1
1
0
FC
1
1
0
FC
1
1
0
FC
1
1
0
FC
1
1
0
FC
1
1
0
FC
1
1
0
FC
1
1
0
FC
1
1
0
FC
1
1
0
FC
1
1
0
FC
1
1
0
FC
1
1
0
FC
1
1
0
FC
1
1
0
FC
1
1
0
FC
1
1
0
FC
1
1
0
FC
1
1
0
FC
1
1
0
FC
1
1
0
FC
1
1
0
FC
1
1
0
FC
1
1
0
FC
1
1
0
FC
1
1
0
FC
1
1
0
FC
1
1
0
FC
1
1
0
FC
1
1
0
FC
1
1
0
FC
1
1
0
FC
1
1
0
FC
1
1
0
FC
1
1
0
FC
1
1
0
FC
1
1
0
FC
1
1
0
FC
1
1
0
FC
1
1
0
FC
1
1
0
FC
1
1
0
FC
1
1
0
FC
1
1
0
FC
1
1
0
FC
1
1
0
FC
1
1
0
FC
1
1
0
FC
1
1
0
FC
1
1
0
FC
1
1
0
FC
1
1
0
FC
1
1
0
FC
1
1
0
FC
1
1
0
FC
1
1
0
FC
1
1
0
FC
1
1
0
FC
1
1
0
FC
1
1
0
FC
1
1
0
FC
1
1
0
FC
1
1
0
FC
1
1
0
FC
1
1
0
FC
1
1
0
FC
1
1
0
FC
1
1
0
FC
1
1
0
FC
1
1
0
FC
1
1
0
FC
1
1
0
FC
1
1
0
FC
1
1
0
FC
1
1
0
FC
1
1
0
FC
1
1
0
FC
1
1
0
FC
1
1
0
FC
1
1
0
FC
1
1
0
FC
1
1
0
FC
1
1
0
FC
1
1
0
FC
1
1
0
FC
1
1
0
FC
1
1
0
FC
1
1
0
FC
1
1
0
FC
1
1
0
FC
1
1
0
FC
1
1
0
FC
1
1
0
FC
1
1
0
FC
1
1
0
FC
1
1
0
FC
1
1
0
FC
1
1
0
FC
1
1
0
FC
1
1
0
FC
1
1
0
FC
1
1
0
FC
1
1
0
FC
1
1
0
FC
1
1
0
FC
1
1
0
FC
1
1
0
FC
1
1
0
FC
1
1
0
FC
1
1
0
FC
1
1
0
FC
1
1
0
FC
1
1
0
FC
1
1
0
FC
1
1
0
FC
1
1
0
FC
1
1
0
FC
1
1
0
FC
1
1
0
FC
1
1
0
FC
1
1
0
FC
1
1
0
FC
1
1
0
FC
1
1
0
FC
1
1
0
FC
1
1
0
FC
1
1
0
FC
1
1
0
FC
1
1
0
FC
1
1
0
FC
1
1
0
FC
1
1
0
FC
1
1
0
FC
1
1
0
FC
1
1
0
FC
1
1
0
FC
1
1
0
FC
1
1
0
FC
1
1
0
FC
1
1
0
FC
1
1
0
FC
1
1
0
FC
1
1
0
FC
1
1
0
FC
1
1
0
FC
1
1
0
FC
1
1
0
FC
1
1
0
FC
1
1
0
FC
1
1
0
FC
1
1
0
FC
1
1
0
FC
1
1
0
FC
1
1
0
FC
1
1
0
FC
1
1
0
FC
1
1
0
FC
1
1
0
FC
1
1
0
FC
1
1
0
FC
1
1
0
FC
1
1
0
FC
1
1
0
FC
1
1
0
FC
1
1
0
FC
1
1
0
FC
1
1
0
FC
1
1
0
FC
1
1
0
FC
1
1
0
FC
1
1
0
FC
1
1
0
FC
1
1
0
FC
1
1
0
FC
1
1
0
FC
1
1
0
FC
1
1
0
FC
1
1
0
FC
1
1
0
FC
1
1
0
FC
1
1
0
FC
1
1
0
FC
1
1
0
FC
1
1
0
FC
1
1
0
FC
1
1
0
FC
1
1
0
FC
1
1
0
FC
1
1
0
FC
1
1
0
FC
1
5`

phord, 2022-12-28:
Yes, I would be interested in seeing a PR to interpret this stream.

Karuption, 2022-12-28:
It seems like most of the interesting values are  4 Bytes in length. Except for the Wake and the end of stream. So looks like using a state machine on those 4 bytes would be good enough for the needed information. I haven't snooped on the controller yet, but would be interesting on how it does things.

Height report: 1 1 X Y (X*256 + Y = Desk Height in the native units * 10)

ASR: 1 4 x01 xAA (Leveling needed, Constantly streams height and then this code)
EO8: 1 2 x80 x00  (Control box error code)
LOC: 1 2 x00 x80  (Lock height)

Wake code: F5
End of stream: 1 5

Sometimes I disconnect my handset and connect the controller it will go into an unknow state (???) then lock the desk height. I assume this is when the handset has a session open and the desk locks the position for safety.
???:  1 6 0 0

phord, 2022-12-28:
On my unit, the **handset** control-lock does not involve the **desk controller** in any way as far as I can tell.  When I lock the **handset**, the display shows a :lock: icon and it stops sending any commands to the **desk controller** except to wake the display (HS3).  It never sends any kind of "LOCK" command to the **desk controller**. In fact, I can unlock the **handset** simply by power-cycling it.

I checked your serial output in the earlier message and confirmed it matches what I saw from my FullyCB2C-A desk controller.  That is, `F5  01 01 {height} 01 01 {height} 01 01 {height} ... 01 01 {height}  01 05`

Does your handset have a display? Does it turn off after the `01 05` is received?  Does it have any "locked" indicator?

Where do the codes come from that you listed, `ASR`, `EO8` and `LOC`?  Are those displayed on the handset?

Karuption, 2022-12-29:
I have been mostly using a cut cable for my troubleshooting, but I have a proper passthrough breakout board and logic analyzer  to look at the handset and controller interaction further after vacation.

LOC is what the handset shows when its locked.
ASR (on the handset) or Reset (in the uplift manual) is the programming mode to set limits and units.
EO8 is displayed on the handset and in the manual as a general error code.

Karuption, 2023-03-04:
Feature added in PR #27. Closing issue.

Closed 2023-03-04.

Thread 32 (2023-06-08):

Wire to Board matching for re-solder

jamesrmaher, 2023-06-08:
**To be up front: This is a question unrelated to your code, but I would gladly buy you a coffee or beer in exchange for some help.**

The work you’ve done here is super impressive. It’s also the only place where I have found more info on the Jarvis handset internals.

Long story short: my handset cord was unfortunately ripped out of the handset. So now the desk is not controllable. I have the board taken out of the handset, and the wires from the ethernet(?) crimped and ready to re-solder to regain control.

The question: Which wire goes on which socket?  I have a red, red/brown, white, transparent and purple wire. The board has LED, M1+, M1-, 5V, GND. Do you know which wire is for which socket? Thanks in advance
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

phord, 2023-06-09:
Bummer! Is this the "Up/Down" controller?  I'm not sure what the "LED" pin would connect to. There's no signal on the interface that makes sense to me for that one.  Also, the purple wire is very short.  Maybe the LED pin was never connected to a wire?

Do you have a multimeter and a soldering iron?

If the "ethernet" RJ-45 connector is the same as mine, then you can find the wire purpose using the continuity test feature of your multimeter. Use this diagram to identify the pin numbers  (Ignore the wire colors on this diagram.)
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

I assume M1+ and M1- are the Up and Down buttons, respectively.  I have no idea what the LED is for.  But if I'm right, then M1+ should go to HS1 and M1- should go to HS0.

Using this assumption, here's what I would do:

1. Touch the meter to pin 3 of the RJ-45 connector.
2. Touch the other lead from your meter to each of the loose wires until you find the one that connects to pin 3 (beep!).  The one that goes to pin 3 should be GND.
3. Next, find the wire that goes to pin 5.  This should be 5V.
4. Confirm that you didn't get the pins backwards by measuring the voltage from the desk when the wire is plugged in.
 a. Set the mulitimeter to measure DC Voltage.
 b. Touch black to GND and red to 5V.
 c. If it shows 5V (or close to it), then you were right! \o/
 d. If it shows -5V, you got the backwards.  (This is also a win. yay!)
5. Continue like this to find the M1+ on pin 6 (HS1) and the M1- on pin 7 (HS0)

If yours isn't wired like mine, then you have some sleuthing to do.  Again, I would do this:

1. Find the ground wire.  One of these 5 wires is the signal ground.  With the cable plugged in to the desk, use a multimeter to measure the voltage between the 9 pairs of wires (white-red, white-purple, white-clear, white-pink, red-purple, red-clear, etc.).  You should find 5v between several of the wires and the ground one.  The ground will be the zero-volt wire.
2. Identify the power wire.  This may be harder because probably 3 or 4 of the non-ground wires will show "5v" when you test with the ground wire.  If you have a resistor handy (at least 100 ohms), use it to connect one of the wires to ground.  If the desk moves down, that's probably M1-.  If it moves up, that's M1+.  If it doesn't move at all, that's either 5V or LED.
7. Identify 5V line.  Using the current meter (ammeter) on your multimeter, you can measure the current through your 100ohm (or whatever size you have) resistor. To do that, you'd connect the ammeter ground to the identified ground wire.  Connect the ammeter positive (or load) to the resistor. (Note: this might be a different connection than you use for Volts on your multimeter). Then touch the other resistor leg to each of the unidentified wires in turn.  The one that passes the most current through your ammeter is going to be the 5V wire.

The last wire is still a mystery to me.  Does it connect to LED?  To something else?

More notes:  If you want to confirm what M1+ and M1- do, you can test the board itself.  Try pressing the Up button while measuring the continuity between the M1+ pin and GND.  If I'm right, pressing Up should cause M1+ to connect to GND, electrically. I think this will work without any power on the board at all.  Repeat this with the Down button and M1-.

What about LED?  Still no clue.  Maybe you can find some ideas by testing continuity between that pin and other solder "pads" on the board.

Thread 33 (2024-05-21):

IKEA MITTZON not receiving commands

Pereira98, 2024-05-21:
I bought a pair of IKEA MITTZON Desks and I'm testing this protocol. I can read the desk position when I manually move it via the handset but when I send commands nothing happens. It's worth pointing out that I'm using the RJ-12 port not the RJ-45 port. Through the FCC files, I can see that Jiecang has a new BT adapter that uses 5 pins so I checked the 5'th wire and it reads 3.3V. This wire is labelled in the BT adapter as "BKG". I'm not sure how to proceed from here since I don't own a BT adapter myself other than use the RJ45 port, but if someone can provide help I would rather use the RJ12 port.

Link for the BT adapter I'm talking about:
https://fcc.report/FCC-ID/2ANKDJCP35NBLT1
(Not sure if this BKG pin is relevant to my problem)

Pereira98, 2024-05-21:
Sorry for the inconvenience, I just forgot to connect the ground of my pico to the desk, was just connected via usb and the TX RX, when I connected the rj12 ground to the pico, it worked fine

I think I found some more commands in the way, I'll confirm my findings and share

phord, 2024-05-24:
Nice finds. How did you determine those commands?

Pereira98, 2024-05-25:
I decompiled the app and searched

OkhammahkO, 2024-05-25:
Very nice work on that!
My desk stops if it's in motion and you press any button.
I might revisit the rj12 port sometime in light of this...
Is there a "go to ad hoc height x" command?

Pereira98, 2024-05-25:
From my understanding the protocol in the rj12 port is not as complete, so not everything that is possible with the rj45 port is possible on the rj 12, but it works for me for what I want and seems safer since the manufacturer uses this port for this effect, Im running a raspberry pi pico w with esphome

I can paste let me check my pc, just gonna take some time

OkhammahkO, 2024-05-25:
I don't believe the rj45 port has a "go to x" command either - you have to roll your own.

The Desky ESPHome project implements one but you lose the "soft start/stop" that the presets have (which is nice), and we didn't figure that out yet.

Pereira98, 2024-05-25:
I think i can figure that one out when i have time and also a sync function since i have 2

Here's the codes
`public static final String cmdDown = "F1F10200027E";
public static final String cmdFetchAllTime = "F1F1AA00AA7E";
public static final String cmdFetchHeightRange = "F1F10C000C7E";
public static final String cmdFetchHeightValue = "F1F10700077E";
public static final String cmdFetchHighestLowestLimit = "F1F12000207E";
public static final String cmdFetchStandTime = "F1F1A60100A77E";
public static final String cmdGotoMemory1 = "F1F10500057E";
public static final String cmdGotoMemory2 = "F1F10600067E";
public static final String cmdGotoMemory3 = "F1F12700277E";
public static final String cmdMemory1 = "F1F10300037E";
public static final String cmdMemory2 = "F1F10400047E";
public static final String cmdMemory3 = "F1F12500257E";
public static final String cmdPatch = "F1F1A000A07E";
public static final String cmdStop = "F1F12B002B7E";
public static final String cmdUp = "F1F10100017E";`

Pereira98, 2024-05-25:
I was curious so i think i found how to send the desk to a desired height but i haven't tested, this is interesting nevertheless
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

OkhammahkO, 2024-05-25:
@Pereira98 are you aware of this ESPHome project?

Maybe we can look to extend it?

I'm a key user (thread OP) but not the developer of the custom component.

https://community.home-assistant.io/t/desky-standing-desk-esphome-works-with-desky-uplift-jiecang-assmann-others/383790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

Pereira98, 2024-05-25:
Yes i can post more info on this but right now i dont have much time, i want to 3d print a case for the pico also, maybe in a few days i can work more on this

I was posting here because phord has great info on the desk and I mostly used the info that he provided, but i didnt use his code, I just made a esphome config

Once I have the time Ill compile my findings and share with you all

OkhammahkO, 2024-05-25:
Yeah no prob at all. No rush. Agree the info here on this project is the best;)

Pereira98, 2024-05-25:
> I was curious so i think i found how to send the desk to a desired height but i haven't tested, this is interesting nevertheless ![Screenshot_20240525_023206_Samsung Internet](https://private-user-images.githubusercontent.com/50386189/333761043-42b762fd-bf12-4d1d-be9f-65fa8b950536.jpg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)
>
> If this does what i think it does, should fix the soft stop problem about go to height, but i haven't tested at this point

I can confirm that this is the go to specific height command, and it does the soft stop thing, via the rj 12 port

Pereira98, 2024-05-25:
Also i think this cmd is to set the memories to specific heights regardless of the desk position, this one i havent tested but its a F1F1A cmd so its a patch cmd that means it changes settings of the desk controller

Pereira98, 2024-05-25:
https://gitlab.com/pimp-my-desk/desk-control

I've started to compile the info I know here

OkhammahkO, 2024-05-26:
I had an initial tinker @Pereira98  and can confirm these are working on my rj12 port.

```
button:
  - platform: uart
    name: "Raise"
    data: [0xF1, 0xF1, 0x01, 0x00, 0x01, 0x7e]
  - platform: uart
    name: "Stop"
    data: [0xF1, 0xF1, 0x2B, 0x00, 0x2B, 0x7E]
  - platform: uart
    name: "Lower"
    data: [0xF1, 0xF1, 0x02, 0x00, 0x02, 0x7e]
  - platform: uart
    name: "Go To Memory 1"
    data: [0xF1, 0xF1, 0x05, 0x00, 0x05, 0x7e]
  - platform: uart
    name: "Go To Memory 2"
    data: [0xF1, 0xF1, 0x06, 0x00, 0x06, 0x7e]
  - platform: uart
    name: "Go To Memory 3"
    data: [0xF1, 0xF1, 0x27, 0x00, 0x27, 0x7e]
  - platform: uart
    name: "Go To Memory 4"
    data: [0xF1, 0xF1, 0x28, 0x00, 0x28, 0x7e]
```

Pereira98, 2024-05-27:
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

I feel this is not the correct place for this discussion, I don't mean this repository but this issue page itself, so I'll continue the discussion in the HA Forum

Closed 2024-05-21.

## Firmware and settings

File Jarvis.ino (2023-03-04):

#include <ArduinoOTA.h>
#include <ESP8266WiFi.h>
#include <ESP8266mDNS.h>
#include <WiFiUdp.h>

#include "local-config.h"
#include "src/JarvisDesk.h"
#include "src/Ota.h"
#include "src/TelnetLogger.h"

#include "AdafruitIO_WiFi.h"
const int LED_PIN = LED_BUILTIN;

AdafruitIO_WiFi io(IO_USERNAME, IO_KEY, WIFI_SSID, WIFI_PASS);
AdafruitIO_Group *jarvis_sub = io.group("jarvis");

JarvisDesk Jarvis;
Ota ota;

// FIXME: Move to flasher.h
void flash(unsigned count = 0, float secs = 0.3);

void setup() {
  pinMode(LED_PIN, OUTPUT);

  io.connect();

  Jarvis.begin();

  jarvis_sub->onMessage("preset", handlePreset);

  flash(0, 0.5);
  while (io.status() < AIO_CONNECTED) {
    delay(100);
  }

  flash(10, 0.1);

  ota.begin();

  LogServer.begin();
  jarvis_sub->get();
}

void loop() {
  // Run the AdafruitIO Service
  io.run();

  // run the Jarvis desk interface
  Jarvis.run();

  LogServer.run();

  // Run the OTA Updater Service
  ota.loop();
}

// Handle messages from AdafruitIO
void handlePreset(AdafruitIO_Data *data) {
  Log.println(">MSG: ", data->feedName(), "=", data->toString());

  auto preset = data->toInt();
  flash(preset, 0.25);

  // Press the button
  Jarvis.goto_preset(preset);
}

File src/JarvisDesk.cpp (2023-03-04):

#include "Arduino.h"

#include "AdafruitIO_WiFi.h"
#include <ESP8266WiFi.h>
#include <SoftwareSerial.h>

#include "JarvisDesk.h"
#include "ProtocolFully.h"
#include "ProtocolUplift.h"
#include "TelnetLogger.h"
#include "jarvis_pinouts.h"

extern AdafruitIO_WiFi io;

enum JarvisMessage {
  BUTTON_DOWN = 1,
  BUTTON_UP = 2,
  BUTTON_1 = 3,
  BUTTON_2 = 4,
  BUTTON_3 = 5,
  BUTTON_4 = 6,
  BUTTON_MEM = 9
};

SoftwareSerial deskSerial(DTX);
SoftwareSerial hsSerial(HTX);

struct one_shot_timer {
  void reset(unsigned long t_ = 1000) { t = millis() + t_; }
  bool trigger() {
    auto now = millis();
    if (t && now - t <= t - now) {
      t = 0;
      return true;
    }
    return false;
  }

  // Timer is set and has not triggered (will trigger)
  bool pending() { return t && !trigger(); }

  // Timer is not set or has expired (will trigger)
  bool expired() { return !pending(); }

  // Timer is set (won't trigger)
  bool active() { return !!t; }

  unsigned long t = 0;
};

class JarvisDesk_impl {
public:
  void begin() {
    jarvis = io.group("jarvis");
    if (is_pin_connected(DTX))
      deskSerial.begin(9600);
    if (is_pin_connected(HTX))
      hsSerial.begin(9600);

    // Disable pullups turned on by espSoftwareSerial library
    if (is_pin_connected(DTX))
      pinMode(DTX, INPUT);
    if (is_pin_connected(HTX))
      pinMode(HTX, INPUT);
    jarvis->get();
  }

  void run() {
    //-- Process signals from desk controller
    decode_serial();

    //-- Manage any pending preset presses
    if (pending_preset) {
      if (is_moving()) {
        if (!pending_stop) {
          // Press the wake sequence once to try to stop our motion
          press_memory(30);
          pending_stop = true;
        }
      } else {
        latch(pending_preset);
        latch_timer.reset();
        pending_preset = 0;
      }
    } else
      pending_stop = false;

    if (latch_timer.trigger()) {
      unlatch();
    }

    // Publish pending updates periodically to AdafruitIO
    io_send();
  }

  void press_memory(int duration = 30) {
#if not defined(JCB35N2PA32V2) // JCB35N2PA32V2 doesn't use this line when pressing memory
    latch_pin(HS0);
#endif
    latch_pin(HS3);
    latch_timer.reset(duration);
    Log.println("Pressing memory for ", duration, "ms");
  }

  bool goto_preset(int p) {
    if (!p || p > 4)
      return false;
    if (p == preset)
      return false;
    pending_preset = p;
    return true;
  }

  void reset(int duration = 5000) {
    // Press and hold down for duration default 5s
    latch_pin(HS0);
    latch_timer.reset(duration);
    Log.println("Starting reset");
  }

  bool readPin(int pin) {
    if (is_pin_connected(pin)) {
      return digitalRead(pin);
    }
    return true; // pretend NC pins are pulled up
  }

  JarvisMessage getMessage() {
    unsigned btn =
      !readPin(HS0) * 1 +
      !readPin(HS1) * 2 +
      !readPin(HS2) * 4 +
      !readPin(HS3) * 8;

    return static_cast<JarvisMessage>(btn);
  }

  bool is_moving() { return height_changed.pending(); }

  void set_preset(unsigned char p) {
    if (preset == p)
      return;
    preset = p;

    // publish update to AdafruitIO
    io_set("preset", p);
  }

  void set_height(unsigned int h) {
    if (h == 9999 || h == 0) {
      Log.print("Fake-height: ");
      Log.println(h);
      return;
    }

    h = Util::to_mm(h);
    if (height == h || h < MIN_HEIGHT || h > MAX_HEIGHT)
      return; // if out of range, ignore it

    height = h;
    height_changed.reset(700);

    // publish update to AdafruitIO
    io_set("height", height);
  }

  void program_preset(unsigned memset) {
    // Record program setting if we know the height
    if (height) {
      char buf[20];
      sprintf(buf, "Prog_%d", memset);
      io_set(buf, height);
    }
    Log.println("Memory-set: ", memset, " ", height);
  }

  unsigned int height = 0;
  unsigned char preset = 0;

  // Timer for last height change (to detect movement)
  one_shot_timer height_changed; // detect active movement
  one_shot_timer latch_timer;    // unlatch a momentary button press
  one_shot_timer io_timer;       // prevent overloading AdafruitIO

  bool io_pending = false;

private:
  AdafruitIO_Group *jarvis = nullptr;

  // The preset we are commanded to go to next, if any
  unsigned char pending_preset = 0;
  bool pending_stop = false;

  void latch_pin(int pin) {
    if (is_pin_connected(pin)) {
      pinMode(pin, OUTPUT);
      digitalWrite(pin, LOW);
    }
  }

  void unlatch_pin(int pin) {
    if (is_pin_connected(pin)) {
      pinMode(pin, INPUT);
      digitalWrite(pin, HIGH);
    }
  }

  void io_set(const char *field, unsigned long value) {
    Log.println("io_set: ", field, "=", value);

    io_pending = true;
    jarvis->set(field, value);

    // Send right away, if possible.
    io_send();
  }

  bool io_send() {
    if (io_pending && io_timer.expired()) {
      Log.print("save:");

      auto data = jarvis->data;
      while (data) {
        Log.print(" ", data->feedName(), "=", data->toString());
        data = data->next_data;
      }
      Log.println();

      jarvis->save();
      io_pending = false;
      io_timer.reset(2000);
      return true;
    }
    return false;
  }

  void unlatch() {
    unlatch_pin(HS0);
    unlatch_pin(HS1);
    unlatch_pin(HS2);
    unlatch_pin(HS3);
  }

  void latch(unsigned preset)
  {
    if (!preset || preset > 4) return;

    // pinout pattern has preset+2
    preset += 2;

    unlatch();
    if (preset & 1) latch_pin(HS0);
    if (preset & 2) latch_pin(HS1);
    if (preset & 4) latch_pin(HS2);
    if (preset & 8) latch_pin(HS3);
  }
#if defined(JCB35N2PA32V2)
  UpliftController deskPacket;
  UpliftController hsPacket;  // unused
#else
  FullyController deskPacket;
  FullyHandset hsPacket;
#endif

  // Decode the serial stream from the desk controller
  void decode_serial() {
    static int msg = 0;

    auto m = getMessage();
    if (m != msg) {
      msg = m;
      LogHs.println("Buttons: ", msg);
    }
    if (is_pin_connected(DTX)) {
      while (deskSerial.available()) {
        auto ch = deskSerial.read();
        LogDesk.print("<");
        LogDesk.print_hex(ch);
        LogDesk.print(">");
        if (deskPacket.put(ch)) {
          deskPacket.decode();
          deskPacket.reset();
          LogDesk.println();
        }
      }
    }

    if (is_pin_connected(HTX)) {
      while (hsSerial.available()) {
        auto ch = hsSerial.read();
        LogHs.print("{");
        LogHs.print_hex(ch);
        LogHs.print("}");
        if (hsPacket.put(ch)) {
          hsPacket.decode();
          LogHs.println();
        }
      }
    }
  }
};

//-- JarvisDesk API interface
JarvisDesk::JarvisDesk() { jarvis = new JarvisDesk_impl(); }

JarvisDesk::~JarvisDesk() { delete jarvis; }

void JarvisDesk::begin() { jarvis->begin(); }

void JarvisDesk::run() { jarvis->run(); }
void JarvisDesk::reset(int duration) { jarvis->reset(duration); }
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

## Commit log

2020-06-14 Add a JarvisDesk module to contain desk code
    Add some serial stream decoders to interpret what the controller
    is sending to the handset. Add a telnet interface to help
    monitor the communications without a logic probe attached.
2020-06-14 Add a 2nd serial feed to list to rx
    Jarvis desk has two serial transmitters, one on the
    controller and one on the handset. To listen to both
    of them, we need two serial interfaces. Fortunately
    the esp8266 has a nice interrupt-driven serial library
    that lets us eavesdrop easily.
    Refactor the serial buffer code so we can reuse it on
    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
2020-06-14 Invert button signal lines for read
    [JarvisDesk.cpp]
2020-06-14 fixup! invert key signal lines
    [JarvisDesk.cpp]
2020-06-14 Add a "stop-moving" step when preset received
    If we're traveling to some new place and a new preset command is
    received, we wait until the traveling stops before commanding the
    new preset. Add a step to try to stop the traveling motion actively
    by pressing the "Memory" button and interrupting the desk's plans.
    Also, shorten our restart delay to 3/4 second instead of 2 seconds.
    [JarvisDesk.cpp]
2020-06-14 Add some serial buffer debug for checksum errors
    We report CHKSUM errors in the serial handler when we get a
    natural EOM 0x7E in the stream, like this height report for 638mm:
    F2-F2-1-3-2-7E-F-93-7E
    Add some code to dump the serial buffer when we see this to help
    confirm it's not really a checksum failure.
    [JarvisDesk.cpp]
2020-06-14 fixup! Separate Group sub and pub objects
    [JarvisDesk.cpp]
2020-06-14 Project layout in new arduino style
    Arduino projects now recognized .cpp files in a src/ subfolder, but all other
    folders are ignored. Move our main sketch up to Jarvis.ino and the other files
    to src/*.cpp instead of the current project name.
    Without this change the VS Code project can't successfully compile all
    the pieces of the project.
2020-06-14 parse correct height despite units
    Determine actual height in mm regardless of units configured.
    Also, ignore bogus height-report values (0, 9999) used
    in some command signaling.
    [JarvisDesk.cpp]
2020-06-14 fix memory leak (not really)
    [JarvisDesk.cpp]
2020-06-14 fixup! to_mm forgot to return anything
    [JarvisDesk.cpp]
2020-06-14 Cleanup: lots of log changes and debug flow
2021-03-05 update VCC label
    I was wondering if the label for 5vdc should be VCC and not GND?
2022-01-23 readme: Add software notes and general cleanup
    Add notes on how to build and use the software. Also add some hints about
    board construction based on questions that have been asked in the discussions.
    Put my Oak build notes in the readme so I won't lose them in the future.
2022-01-23 Oak wiring: Change pins for HS2/HS3
    I found that the Wemos D1 Mini can be dropped in-place for my
    Digistump Oak board, but some of the reulting GPIO pins are
    inconveniently mapped. Move HS2 and HS3 to new pins on the Oak
    to simplify this transition to the D1 Mini.
2022-01-24 Move to Wemos D1 mini hardware
    Changed the target board and pinouts for a Wemos D1 mini. This board
    fits into the same carrier board I originally built, but the GPIOs are all
    different and the board is flipped over in the other direction.
    [JarvisDesk.cpp]
2022-02-11 Cleanup pin definitions and move them their own header
    Add a macro to make definitions more compact so we can reasonably track
    multiple different targets in the current code.
2022-02-12 Add circuit board design files
    [JarvisDesk_WeMosD1Mini_v2.fzz]
2023-02-25 Interpret "wake" button better.
    I noticed the HS3+HS0 signal is always sent to wake the
    display. This makes sense because the display otherwise
    is dark. Update the README to reflect this.
2023-02-25 Send more events to the debug log
    Log desk commands like "<xx><xx>..." and handset commands like "{xx}{xx}...". Also show keypress "messages"
    in square brackets.
2023-03-01 Fix: wrong pin checked in decode_serial
    We tried to test if the handset was connected, but we checked the
    desk instead.
    [JarvisDesk.cpp]
2023-03-02 Refactor serial protocol into separate files
    Extract the protocol code out of the JarvisDesk struct so it can be more easily
    managed, extended, and replaced. In particular this should make it easier
    for Karuption's <pederson26@gmail.com> change to be incorporated into
    the project as it aims to work with the other protocol seen from time to time
    (and all the time on his desk).
    [JarvisDesk.cpp]
2023-03-02 Simplify "Buttons" message
    No one cares to see a series of button press numbers. Just show the number
    on a single line like any other log.
2023-03-04 refactor TelnetServer out of TelnetLogger
    Separate the print helpers from the telnet server logic so we can create
    more logger instances without conflicting later on.
    Keep some specialized print-helpers in TelnetServer to expose the serverClient
    functionality without having to create another template wrapper for it.
2023-03-04 isolate loggers for desk/handset protocol printing
    Add simple commands to UserCommand to control them:
    hs - toggle handset logging on/off
    desk - toggle desk logging on/off
